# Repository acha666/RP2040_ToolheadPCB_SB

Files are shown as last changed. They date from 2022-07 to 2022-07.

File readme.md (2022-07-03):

# Stealthburner_Toolhead_PCB

<font size=5>[中文文档/Chinese Document](readme_cn.md)</font>

**The Project has not finished**

## Overview
This project contains a 3Dprinter Toolhead PCB for VORON StealthBurner Toolhead

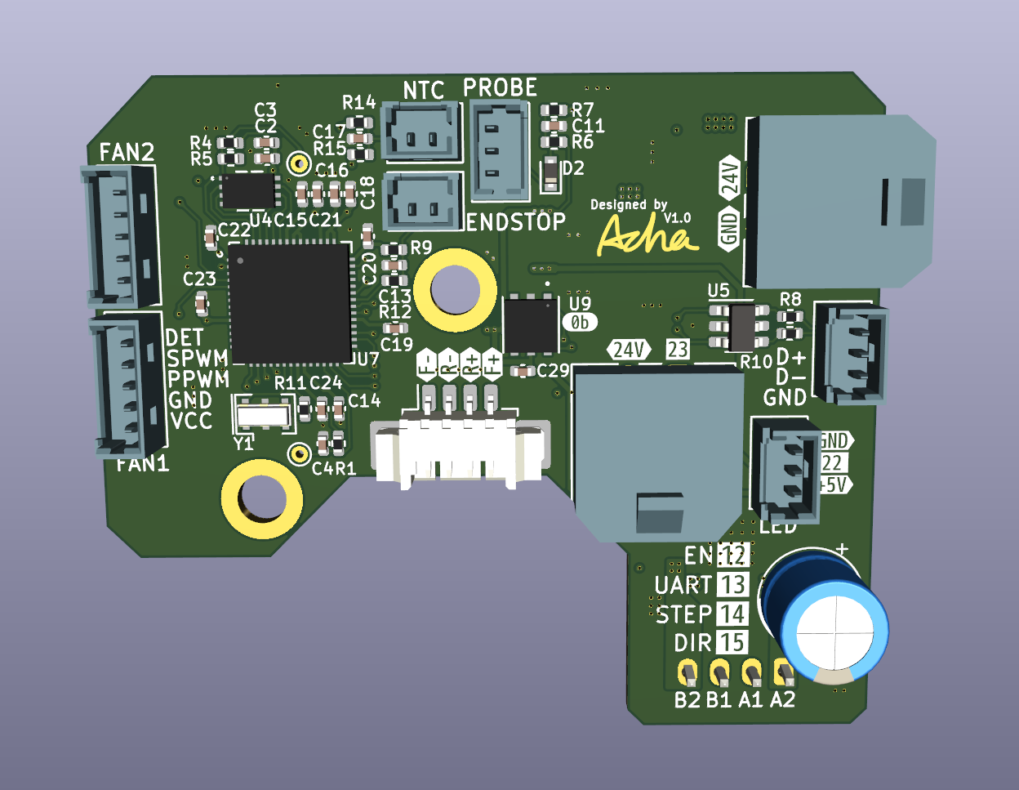
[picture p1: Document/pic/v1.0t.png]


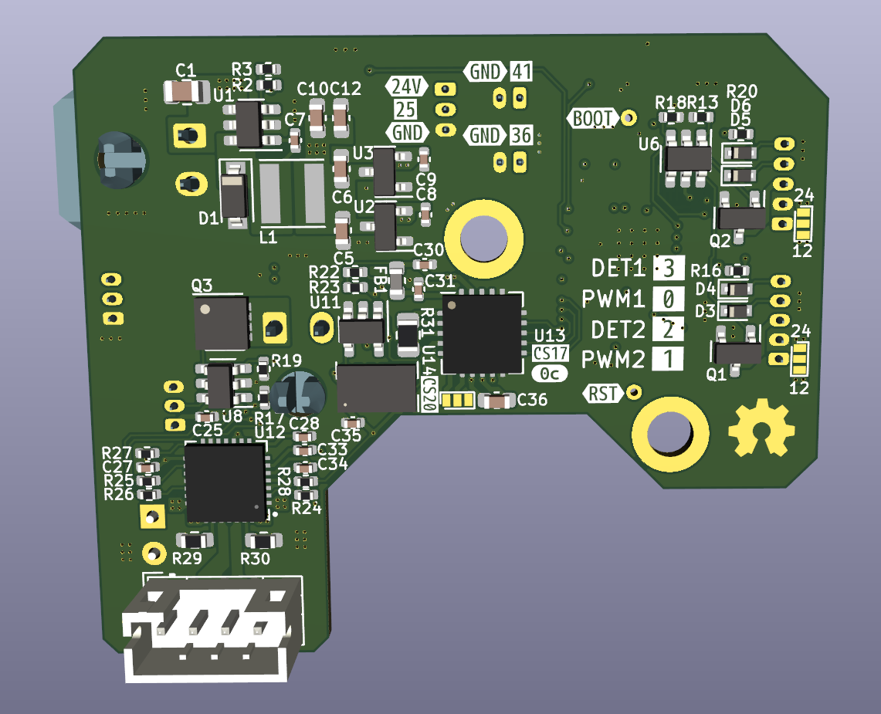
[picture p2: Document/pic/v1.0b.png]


The board has

* RP2040 Microcontroller, connect to Raspberry PI with USB
* TMC2209 for extruder motor
* MAX31865 RTD-to-Digital Converter
* SHT20 humidity&temperature sensor
* ADXL345 accrometer
* Two 5pins fan connecter, fit with 2/3/4 wires, 12/24V fans
* A 3pins probe connecter
* A normal NTC Thermistor connector
* A 2pins X Endstop connector
* A 3pins 5V WS2812(Neopixel) LED connector
* A 24V heater connector

## [Config Referencce](klipper_config.cfg)

## [Programming Guide](Document/programming.md)

## Details
### Microcontroller
You can easily buy a RP2040 chip by about 1USD, it's much cheaper than similar STM32 series MCU today

the RP2040 has some UART interfaces ans a USB port, the USB is used for this design

### MAX31865
the on-board MAX31865 chip supports 2/3/4 wires, PT100/PT1000 RTD. please notice that you should choose the reference resistor(430R/4.3K) and a capacitor(100nF/1uF) based on your RTD value. If you use an 3wire RTD, please connect the FORCE2 pin to PORCE+, otherwise connect it to GND. Please make sure that your wiring is correct. Check the [Datasheet](https://datasheets.maximintegrated.com/en/ds/MAX31865.pdf) and [Here](Document/max31865.md) for more information.

### SHT20
This sensor is used to monitor chamber temp.

Though SHT20 is an NRND product now, we have no choice because klipper frimware only support SHT20. DS18B20 sensors are only supported on the "host mcu". A NTC thermistor should work too, so if a RTD sensor is used to measure hotend temp, you can have a try.

### ADXL345
is for resonances measurement. Both ADXL343 and ADXL345 should work

### FAN Connecter
support 2wires, 3wires(with speed monitor pin), 4wires(with PWM input and speed monitor)

12V/24V voltage can be set by the jumper. Check [Here](Document/fan.md) for more information.

### Heater
be careful about selection on MOSFET, a N-Channel MOSFET with low RDSon at 4.5V

### DC-DC
many models can be used, as long as they have same pin out

The inductor is 4x4mm package, as slim as possible(under 2mm height)

You may choose
* WPN4012H (Sunlord)
* SPH4012S PH4018 (Sunlord)
* SWPA4010 SWPA4018 SWPA4020 (Sunlord)
* SLW4010 (Sunltech)
* FHD4012 (cjiang)

| Buck converter options |
| --- |
| BL9342(by Shanghai Belling) |
| LMR54410(by TI)(Not tested) |
| LMR14006(by TI)(Not tested) |

please check the schmatic for details

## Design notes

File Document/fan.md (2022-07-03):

# Fan Wiring

There are five pins in connecter, they are

* frequency generation waveform input
* PWM **signal** output
* PWM **power** output
* ground
* power

For those fans they have own PWM signal input, the PWM **power** output is unused

# 2 Wires
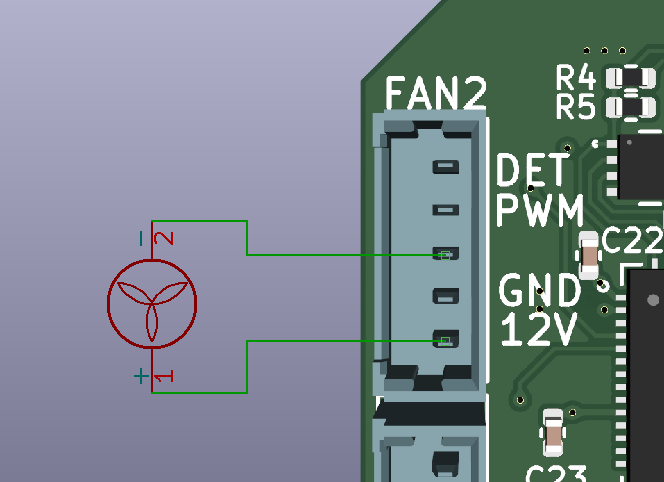
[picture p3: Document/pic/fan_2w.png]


# 3 Wires
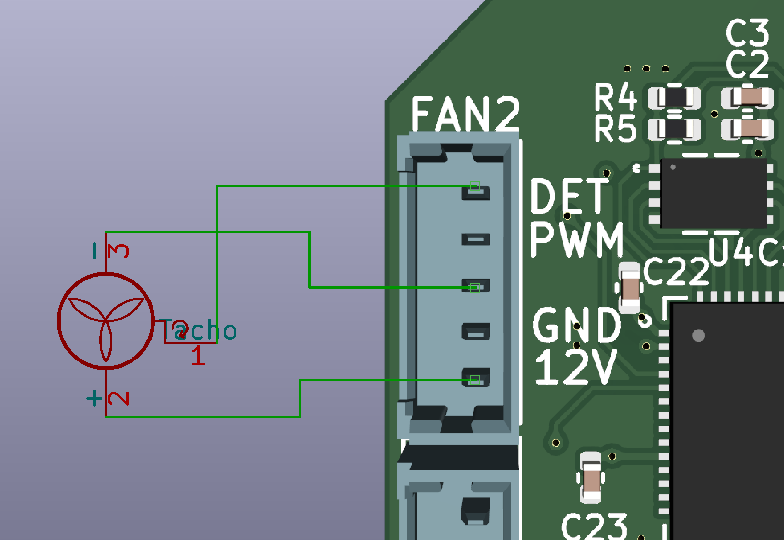
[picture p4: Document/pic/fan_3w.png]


# 4 Wires
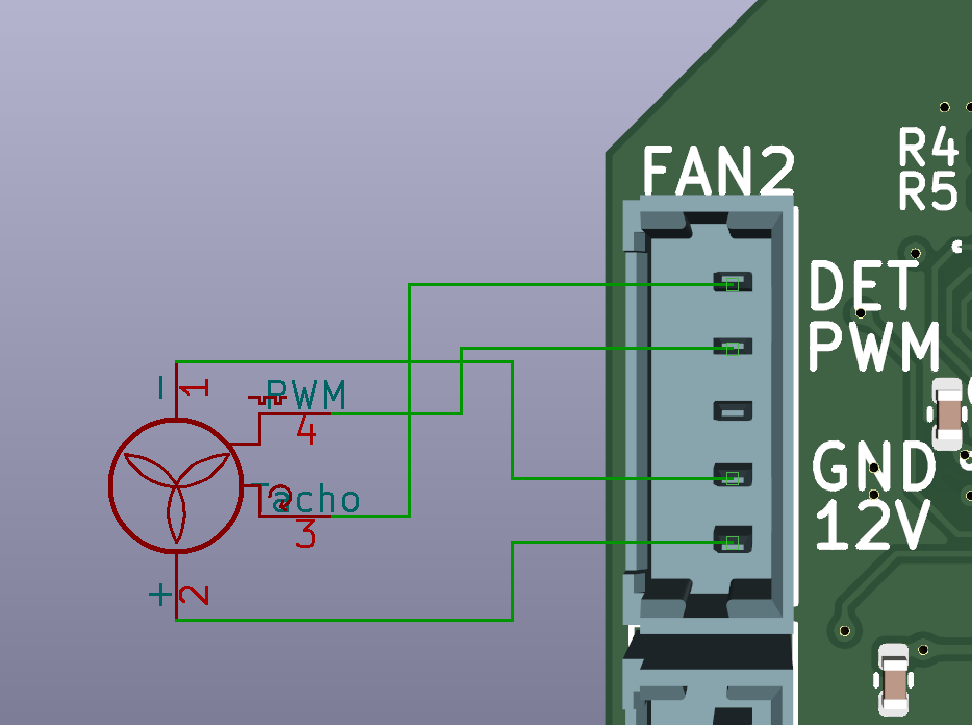
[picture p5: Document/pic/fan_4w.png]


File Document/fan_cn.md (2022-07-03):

# 风扇接线

风扇接口五个引脚，分别是

* 转速检测方波输入
* PWM**信号**输出
* PWM**功率**输出
* 地
* 供电

对于有PWM信号输入的风扇，用不到PWM功率输出的，MOS管等可以不贴

# 二线


# 三线


# 四线


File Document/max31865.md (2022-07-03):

# For Different Wire Number

## 2 Wires
connect Force2 to ground, they are pin2&3 for the jumper

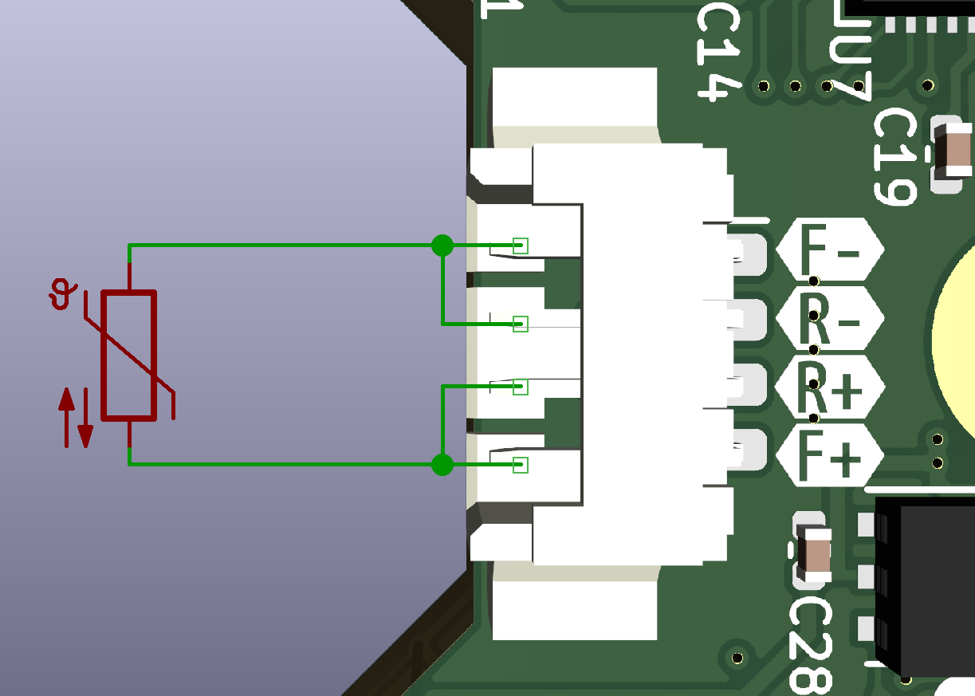
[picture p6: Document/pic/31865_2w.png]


## 3 Wires
connect Force2 to Force+, they are pin1&2 for the jumper

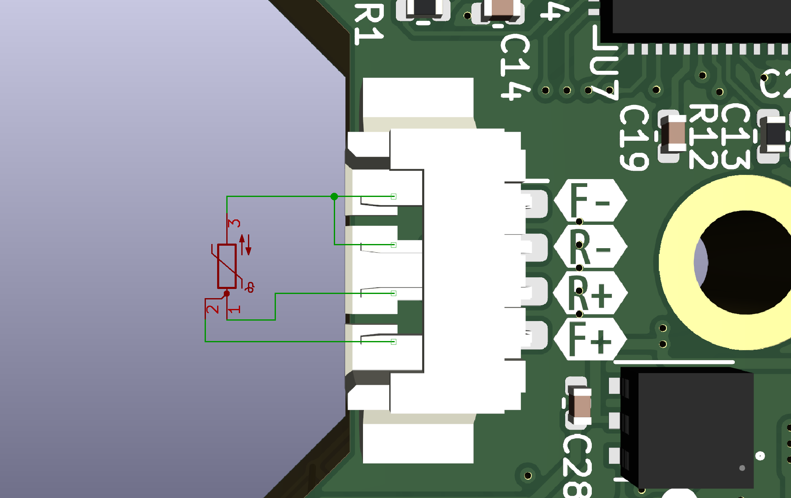
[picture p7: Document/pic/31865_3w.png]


## 4 Wires
connect Force2 to ground, they are pin2&3 for the jumper

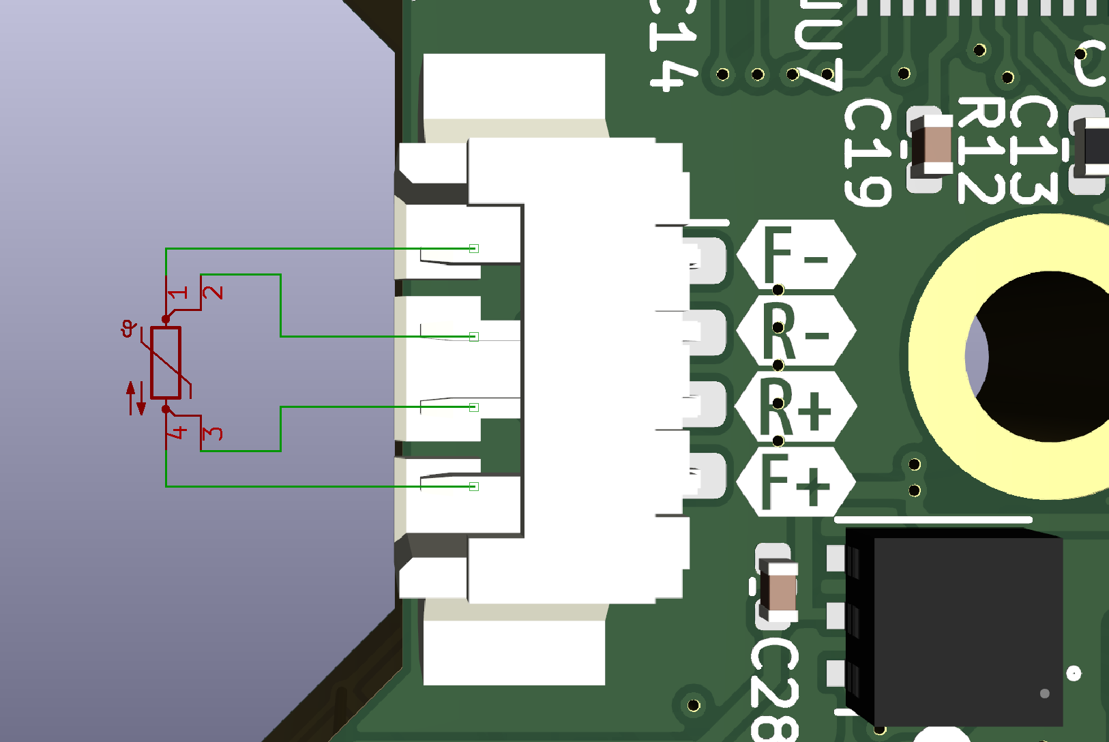
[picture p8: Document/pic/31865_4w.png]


# For Different RTD Value
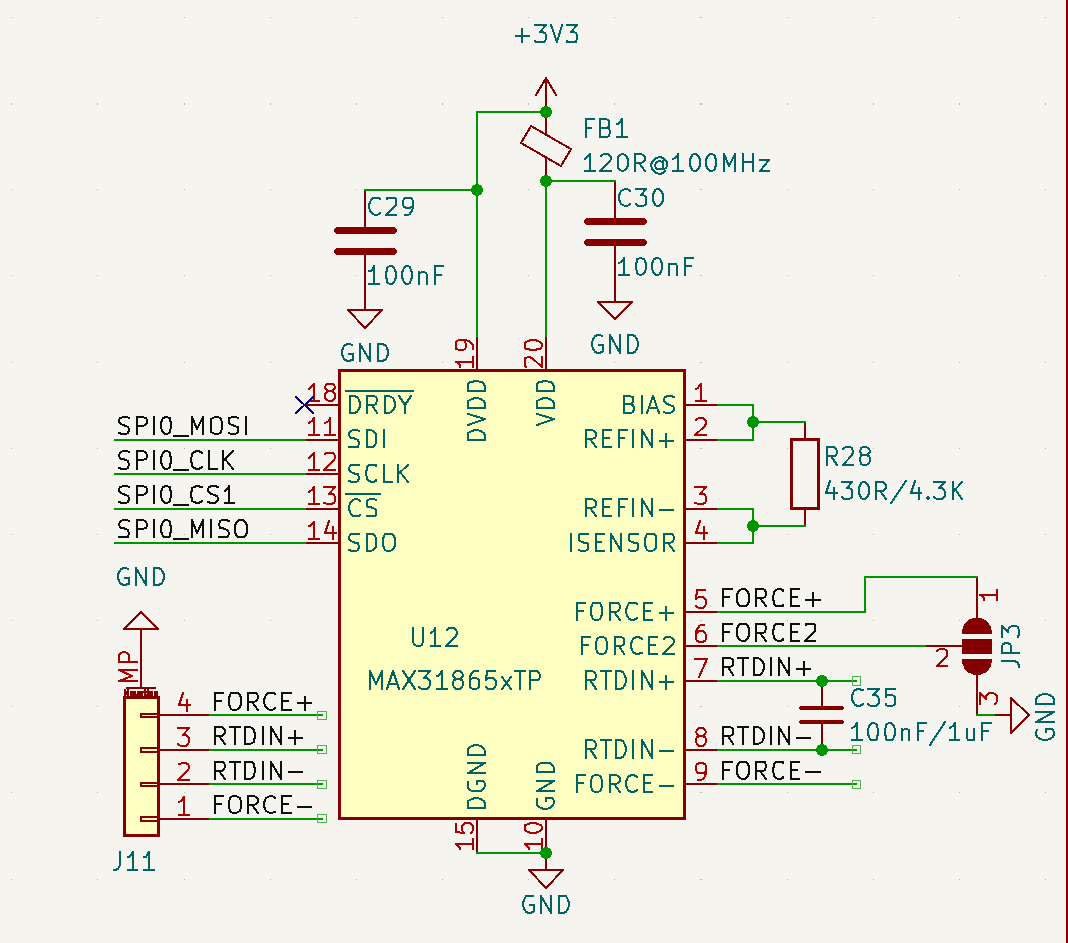
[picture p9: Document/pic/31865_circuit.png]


the R28 in picthre is reference resistor, C35 is the Capacitor

Please choose High-quality, High-precision and Low-temperature-drift resistor

But actually a normal 1% resistor work well too

| RTD | Resistance | Capacitance |
|-----|-----|---|
|PT100 | 430R|100nF|
|PT1000|4.3K|1uF|

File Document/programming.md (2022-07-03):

# Programming

The board has two testpoints, they are for boot select and reset

Connecting the boot testpoint to ground makes mcu boot from bootloader

Connecting the reset testpoint to ground makes mcu reset

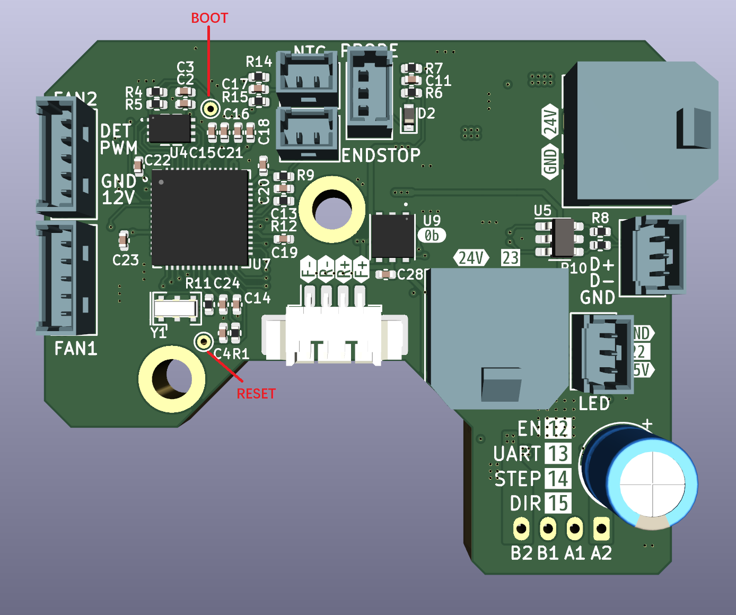
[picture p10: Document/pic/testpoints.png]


Check [User Manual of BigTreeTech SKR-PICO](https://github.com/bigtreetech/SKR-Pico) for more information

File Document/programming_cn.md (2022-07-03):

# 程序烧录

板上引出了复位测试点和启动选择测试点，如图



短接RST到地使MCU复位，在复位时短接BOOT到地启动到Bootloader进行程序烧录

若有疑问请参考[BigTreeTech SKR-PICO 用户手册](https://github.com/bigtreetech/SKR-Pico)

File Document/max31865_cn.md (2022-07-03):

# 不同线制

## 2线
短接Force2到地，即跳线23脚

如图连接



## 3线
短接Force2到Force+，即跳线12脚

如图连接



## 4线
短接Force2到地，即跳线23脚

如图连接



# 不同铂电阻阻值

图中R28为参考电阻，C35为电容

参考电阻请选择高质量、高精度、低温漂的电阻，当然预算有限1%又不是不能用

| 类型 | 阻值 | 容值 |
|-----|-----|---|
|PT100 | 430R|100nF|
|PT1000|4.3K|1uF|

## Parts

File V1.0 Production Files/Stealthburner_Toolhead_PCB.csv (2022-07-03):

Designator | Qnty | Comment | Footprint
C1, | 1 | 22uF/35V | Capacitor_SMD:C_0805_2012Metric
C2, | 1 | 2.2uF | Capacitor_SMD:C_0402_1005Metric
C3, C4, C7, C11, C13, C14, C15, C19, C20, C21, C22, C23, C24, C25, C27, C29, C30, C31, C33, C35, | 20 | 100nF | Capacitor_SMD:C_0402_1005Metric
C5, C6, | 2 | 10uF | Capacitor_SMD:C_0603_1608Metric
C8, C9, C17, | 3 | 10uF | Capacitor_SMD:C_0402_1005Metric
C10, C12, | 2 | 22uF | Capacitor_SMD:C_0603_1608Metric
C16, C18, | 2 | 1uF | Capacitor_SMD:C_0402_1005Metric
C28, | 1 | 4.7uF | Capacitor_SMD:C_0402_1005Metric
C32, | 1 | 100uF | Capacitor_THT:CP_Radial_D6.3mm_P2.50mm
C34, | 1 | 22nF | Capacitor_SMD:C_0402_1005Metric
C36, | 1 | 100nF/1uF | Capacitor_SMD:C_0603_1608Metric
D1, | 1 | CUS10S30 | Diode_SMD:D_SOD-123
D2, | 1 | 1N4148WT | Diode_SMD:D_SOD-523
D3, D5, | 2 | 1N4148 | Diode_SMD:D_SOD-523
D4, D6, | 2 | D_TVS | Diode_SMD:D_SOD-523
FB1, | 1 | 120R@100MHz | Inductor_SMD:L_0603_1608Metric
H1, H2, | 2 | MountingHole | 1_Library:MountingHole_3mm_Pad
J1, J9, | 2 | Conn_01x02 | 1_Library:Molex_Micro-Fit_3.0_43650-0200_1x02_P3.00mm_Horizontal
J2, J5, J8, | 3 | Conn_01x03 | 1_Library:Molex_PicoBlade_53047-0310_1x03_P1.25mm_Vertical
J3, | 1 | TestPoint | TestPoint:TestPoint_THTPad_D1.0mm_Drill0.5mm
J4, J6, | 2 | Conn_01x02 | 1_Library:Molex_PicoBlade_53047-0210_1x02_P1.25mm_Vertical
J7, J10, | 2 | Conn_01x05 | 1_Library:Molex_PicoBlade_53047-0510_1x05_P1.25mm_Vertical
J11, | 1 | Conn_01x04 | Connector_Molex:Molex_PicoBlade_53261-0471_1x04-1MP_P1.25mm_Horizontal
J12, | 1 | Conn_01x04 | Connector_JST:JST_PH_B4B-PH-K_1x04_P2.00mm_Vertical
JP1, JP2, | 2 | SolderJumper_3_Open | 1_Library:SolderJumper-3_P1.3mm_Open_Pad1.0x1.5mm
JP3, | 1 | 1_Library:SolderJumper-3_P1.3mm_Open_Pad1.0x1.5mm | 1_Library:SolderJumper-3_P1.3mm_Open_Pad1.0x1.5mm
L1, | 1 | 6.2uH | Inductor_SMD:L_Taiyo-Yuden_NR-40xx
Q1, Q2, | 2 | AO3400A | Package_TO_SOT_SMD:SOT-23
Q3, | 1 | WSD4038DN | Package_SON:VSON-8_3.3x3.3mm_P0.65mm_NexFET
R1, R6, R9, R13, R16, R17, R18, R19, R20, R22, R23, | 11 | 10K | Resistor_SMD:R_0402_1005Metric
R2, | 1 | 124K | Resistor_SMD:R_0402_1005Metric
R3, | 1 | 8.87K | Resistor_SMD:R_0402_1005Metric
R4, | 1 | NC | Resistor_SMD:R_0402_1005Metric
R5, R11, | 2 | 1K | Resistor_SMD:R_0402_1005Metric
R7, R12, R14, R24, R25, R26, | 6 | 100R | Resistor_SMD:R_0402_1005Metric
R8, R10, | 2 | 27R | Resistor_SMD:R_0402_1005Metric
R15, | 1 | 4.7K | Resistor_SMD:R_0402_1005Metric
R27, R28, | 2 | 20K | Resistor_SMD:R_0402_1005Metric
R29, R30, | 2 | 0R11 | Resistor_SMD:R_0603_1608Metric
R31, | 1 | 430R/4.3K | Resistor_SMD:R_0805_2012Metric
TP1, | 1 | TestPoint | TestPoint:TestPoint_THTPad_D1.0mm_Drill0.5mm
U1, | 1 | BL9342 | Package_TO_SOT_SMD:SOT-23-6
U2, | 1 | ME6209A50M3G | Package_TO_SOT_SMD:SOT-23
U3, | 1 | ME6209A33M3G | Package_TO_SOT_SMD:SOT-23
U4, | 1 | W25Q16JVUXIQ | 1_Library:W25Q16JVUXIQ
U5, | 1 | USBLC6-2SC6 | Package_TO_SOT_SMD:SOT-23-6
U6, U8, | 2 | 74LVC2G17 | Package_TO_SOT_SMD:SOT-23-6
U7, | 1 | RP2040 | 1_Library:RP2040TR7
U9, | 1 | SHT20 | 1_Library:SHT20
U11, | 1 | 74LVC1G32 | Package_TO_SOT_SMD:SOT-23-5
U12, | 1 | TMC2209-LA-T | 1_Library:TMC2209-LA-T
U13, | 1 | MAX31865xTP | Package_DFN_QFN:TQFN-20-1EP_5x5mm_P0.65mm_EP3.25x3.25mm
U14, | 1 | ADXL343 | Package_LGA:LGA-14_3x5mm_P0.8mm_LayoutBorder1x6y
Y1, | 1 | CSTNE12M0 | Crystal:Resonator_SMD_Murata_CSTxExxV-3Pin_3.0x1.1mm

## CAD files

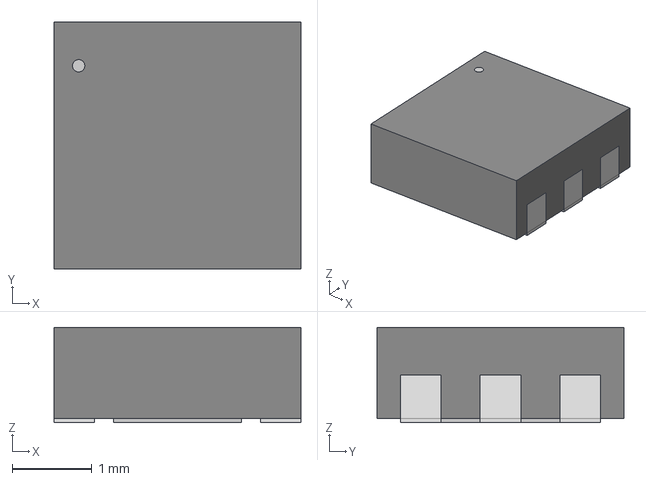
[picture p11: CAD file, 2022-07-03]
Hardware/3D/1-100706-01_SEN.step
3.10 x 3.10 x 1.20 mm

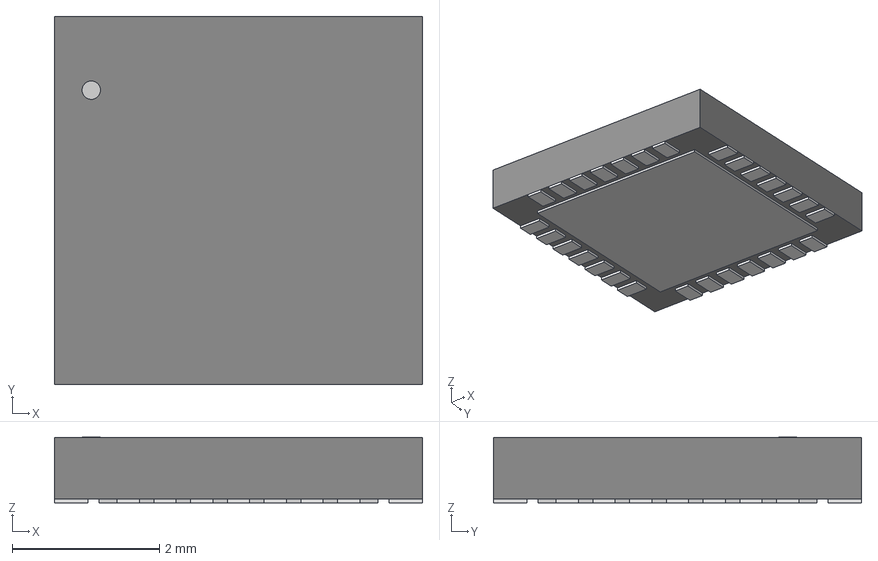
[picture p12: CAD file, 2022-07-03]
Hardware/3D/QFN28_5X5_3X8_EPAD_TRI.step
5.00 x 5.00 x 0.892 mm

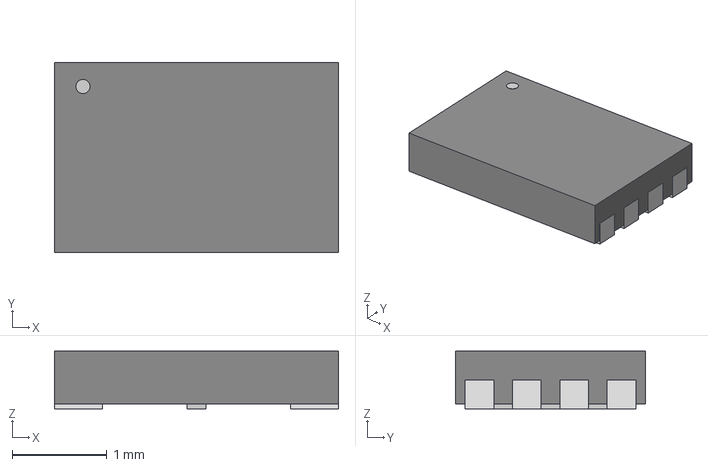
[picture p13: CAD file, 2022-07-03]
Hardware/3D/W25Q16JVUXIQ_WIN.step
3.00 x 2.01 x 0.612 mm

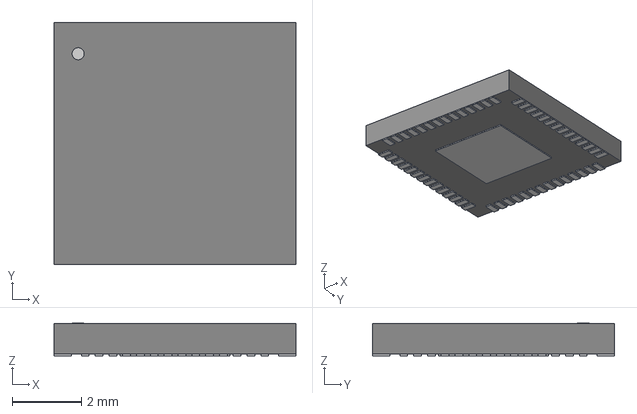
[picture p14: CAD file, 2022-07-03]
Hardware/3D/RP2040TR7_RPI.step
7.01 x 7.01 x 0.942 mm

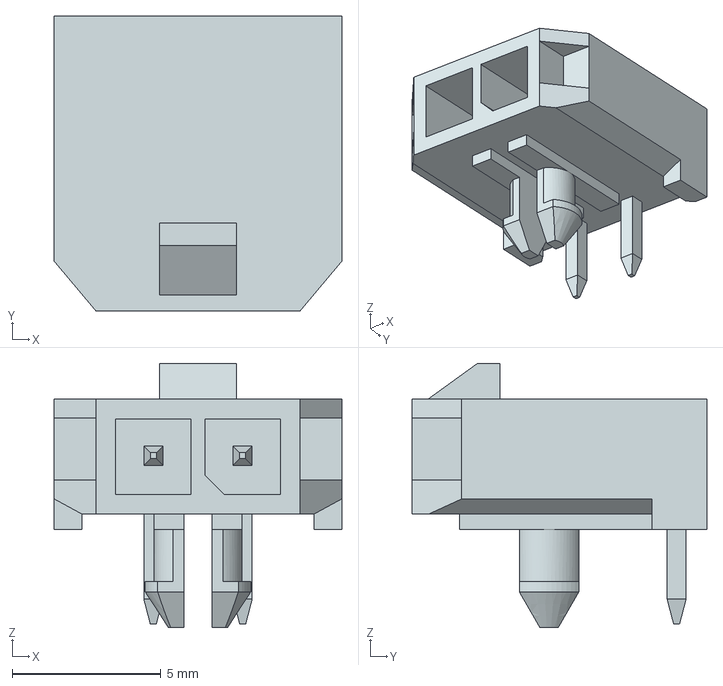
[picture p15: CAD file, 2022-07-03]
Hardware/3D/436500200.stp
9.65 x 9.90 x 8.87 mm

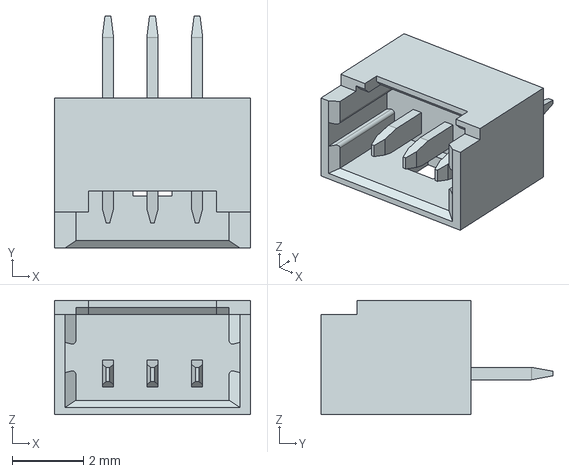
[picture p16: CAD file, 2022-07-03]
Hardware/3D/530470310.stp
5.50 x 6.50 x 3.20 mm

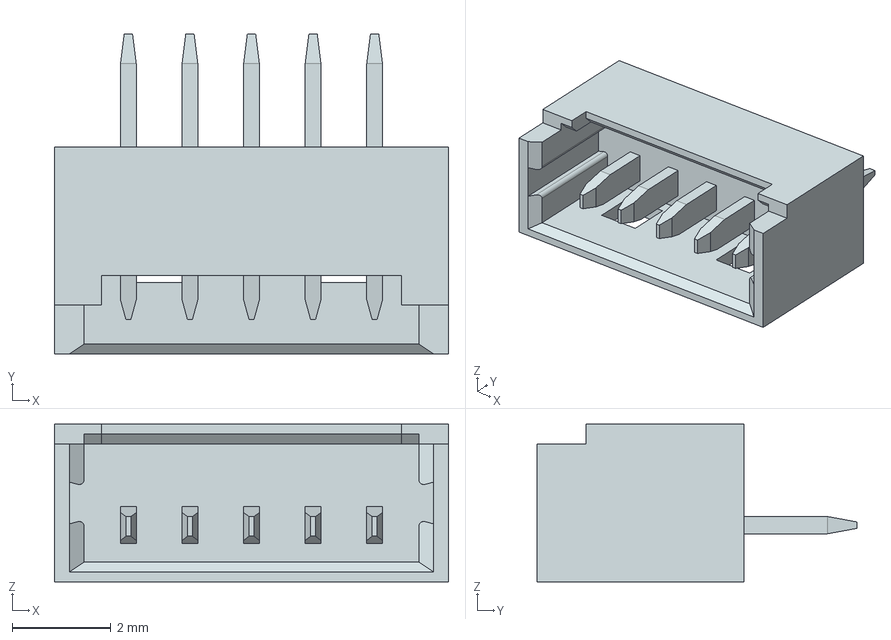
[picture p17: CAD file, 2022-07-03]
Hardware/3D/530470510.stp
8.00 x 6.50 x 3.20 mm

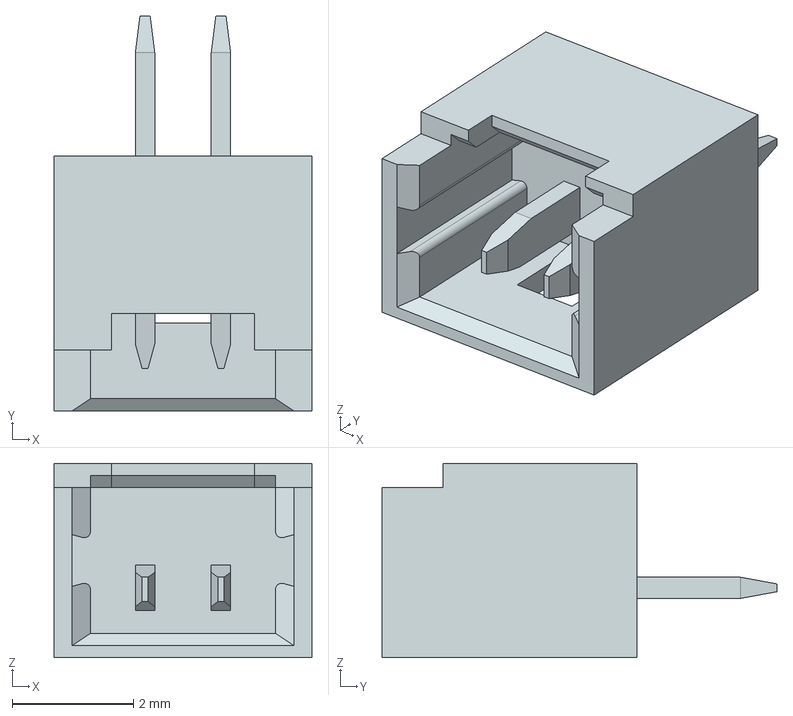
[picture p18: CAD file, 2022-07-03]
Hardware/3D/530470210.stp
4.25 x 6.50 x 3.20 mm

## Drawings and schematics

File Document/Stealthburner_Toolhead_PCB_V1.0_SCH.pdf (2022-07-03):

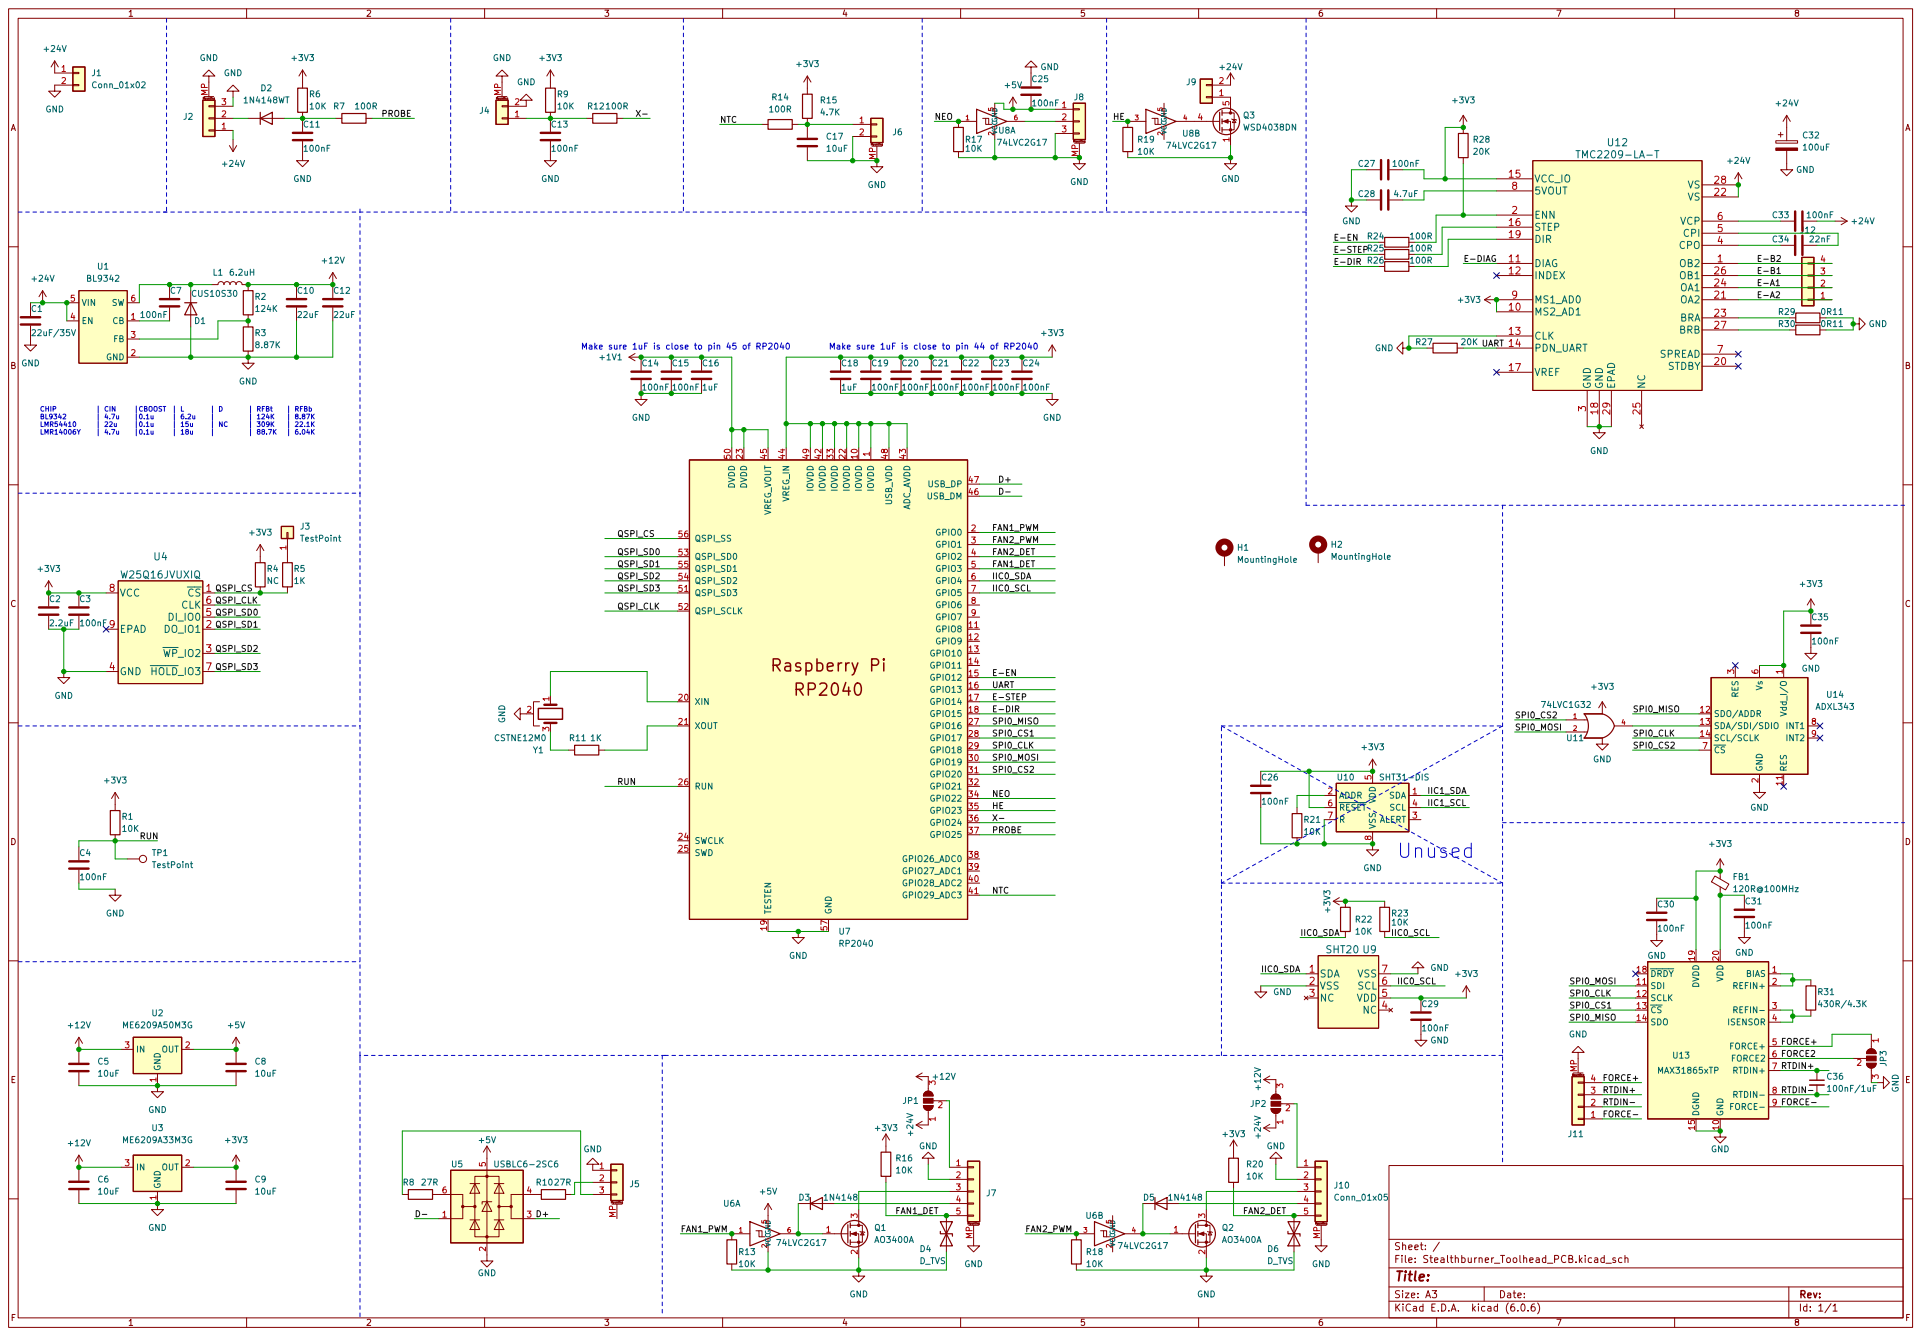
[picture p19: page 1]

CHIP | CIN |CBOOST | L | D | RFBt | RFBb BL9342 | 4.7u |0.1u | 6.2u | | 124K | 8.87K

1 IOVDD 10 GPIO8 11 GPIO9 12 GPIO10 13 GPIO11 14 GPIO12 15 GPIO13 16 GPIO14 17 GPIO15 18 TESTEN 19 GPIO0 2 XIN 20 XOUT 21 IOVDD 22 DVDD 23 SWCLK 24 SWD 25 RUN 26 GPIO16 27 GPIO17 28 GPIO18 29 GPIO1 3 GPIO19 30 GPIO20 31 GPIO21 32 IOVDD 33 GPIO22 34 GPIO23 35 GPIO24 36 GPIO25 37 GPIO26_ADC0 38 GPIO27_ADC1 39 GPIO2 4 GPIO28_ADC2 40 GPIO29_ADC3 41 IOVDD 42 ADC_AVDD 43 VREG_IN 44 VREG_VOUT 45 USB_DM 46 USB_DP 47 USB_VDD 48 IOVDD 49 GPIO3 5 DVDD 50 QSPI_SD3 51 QSPI_SCLK 52 QSPI_SD0 53 QSPI_SD2 54 QSPI_SD1 55 QSPI_SS 56 GND 57 GPIO4 6 GPIO5 7 GPIO6 8 GPIO7 9 U7RP2040 +3V3

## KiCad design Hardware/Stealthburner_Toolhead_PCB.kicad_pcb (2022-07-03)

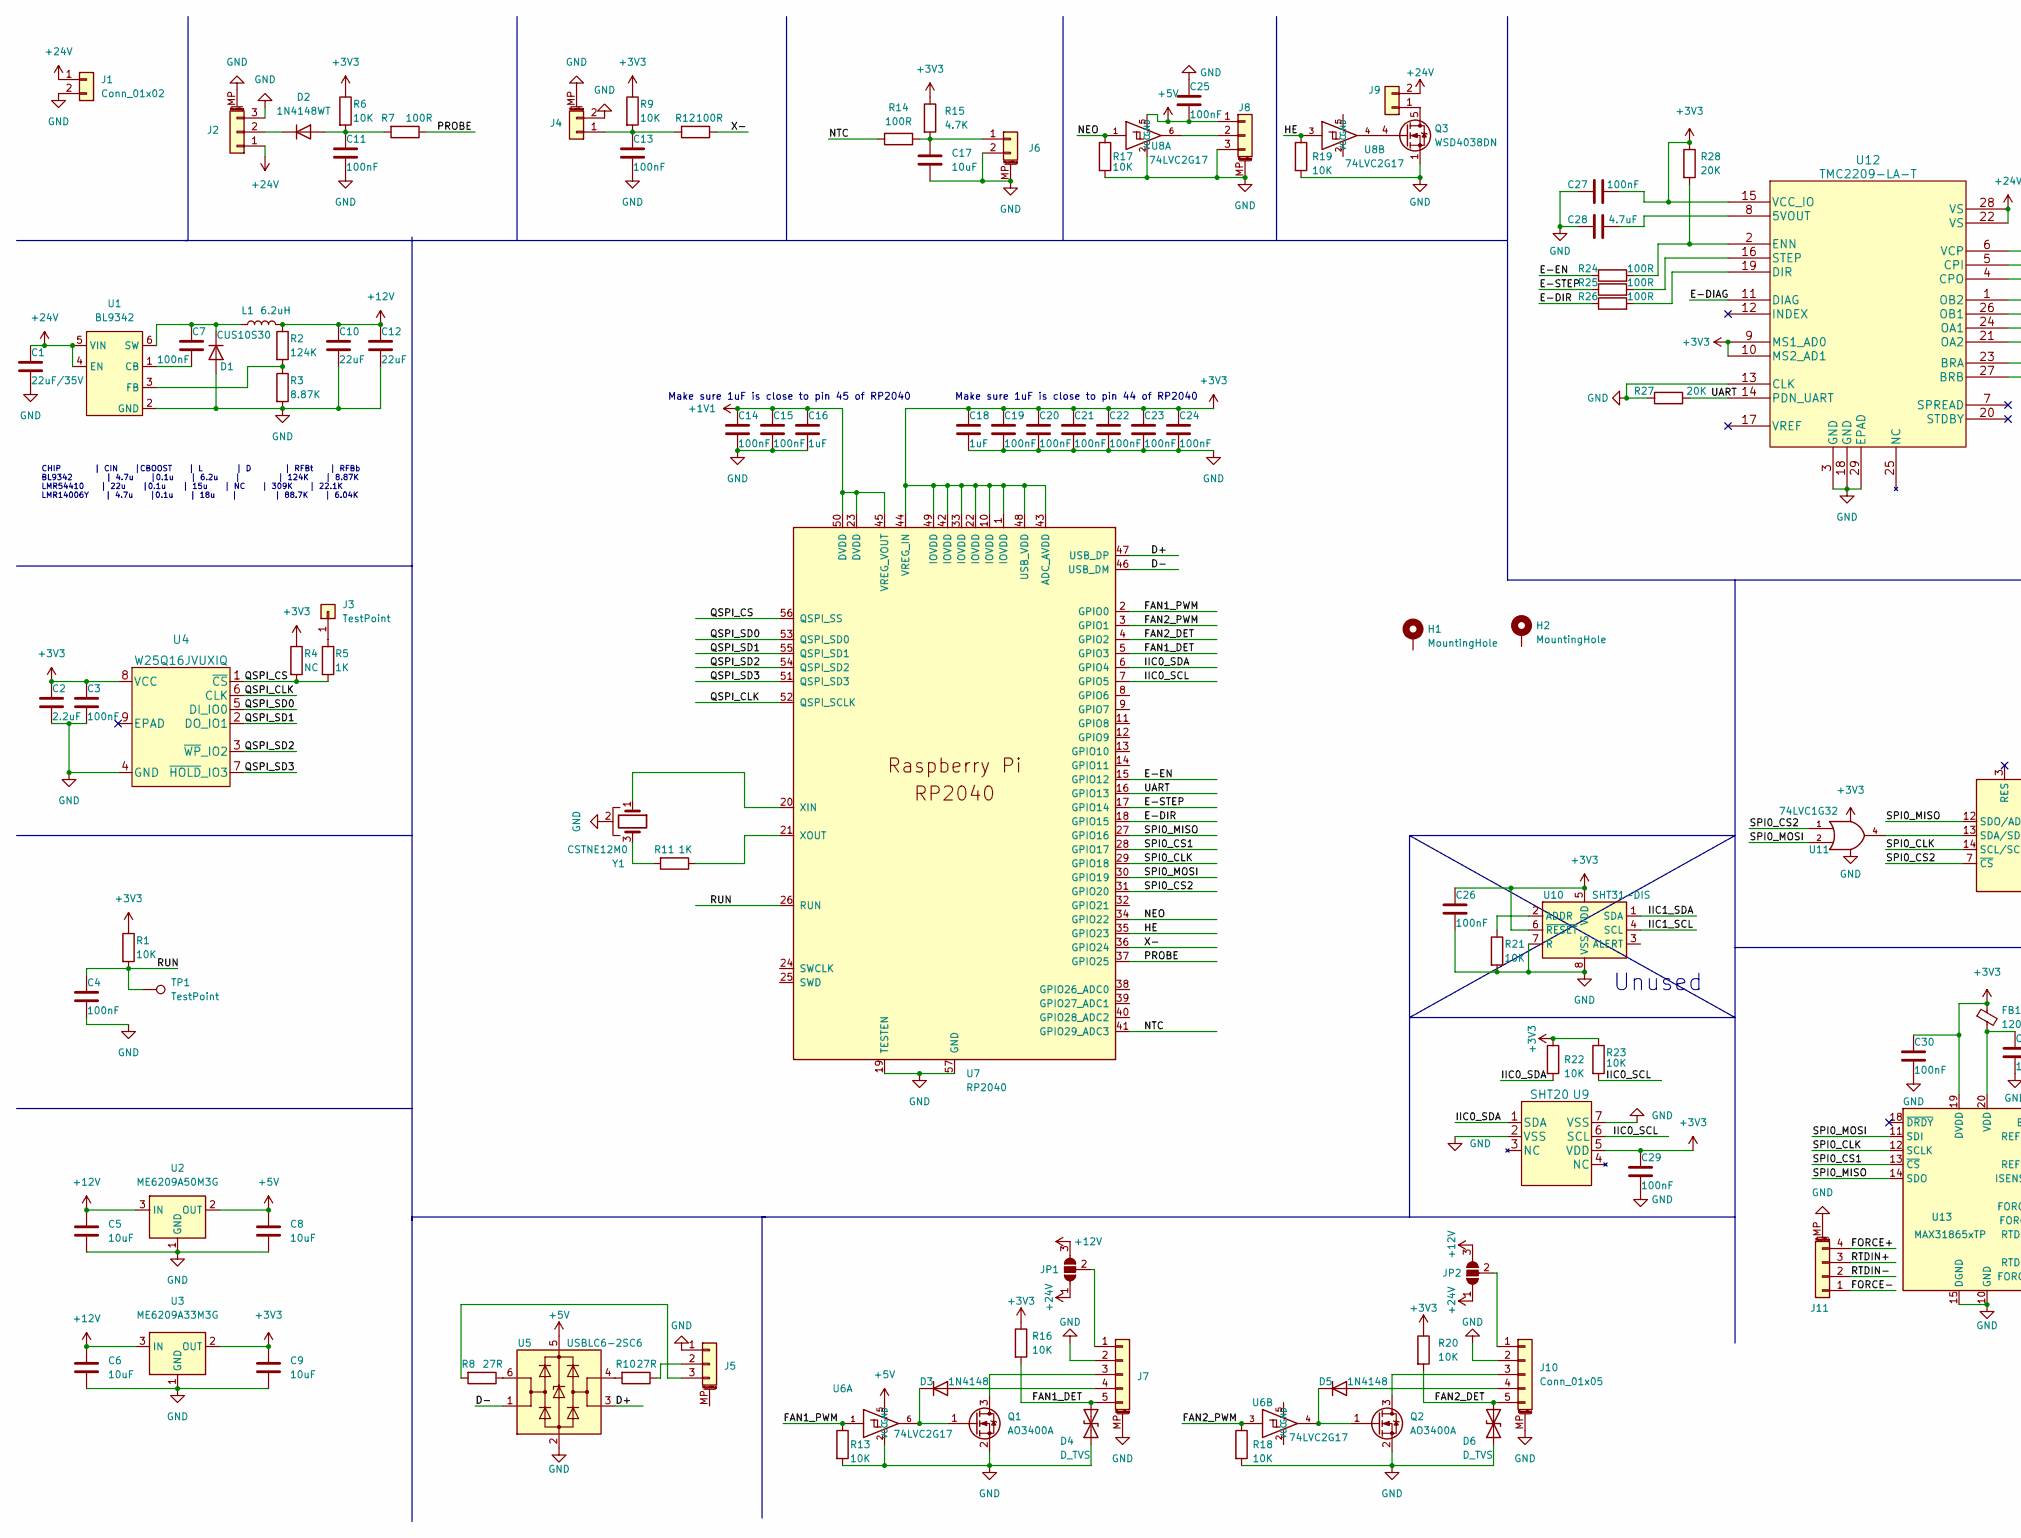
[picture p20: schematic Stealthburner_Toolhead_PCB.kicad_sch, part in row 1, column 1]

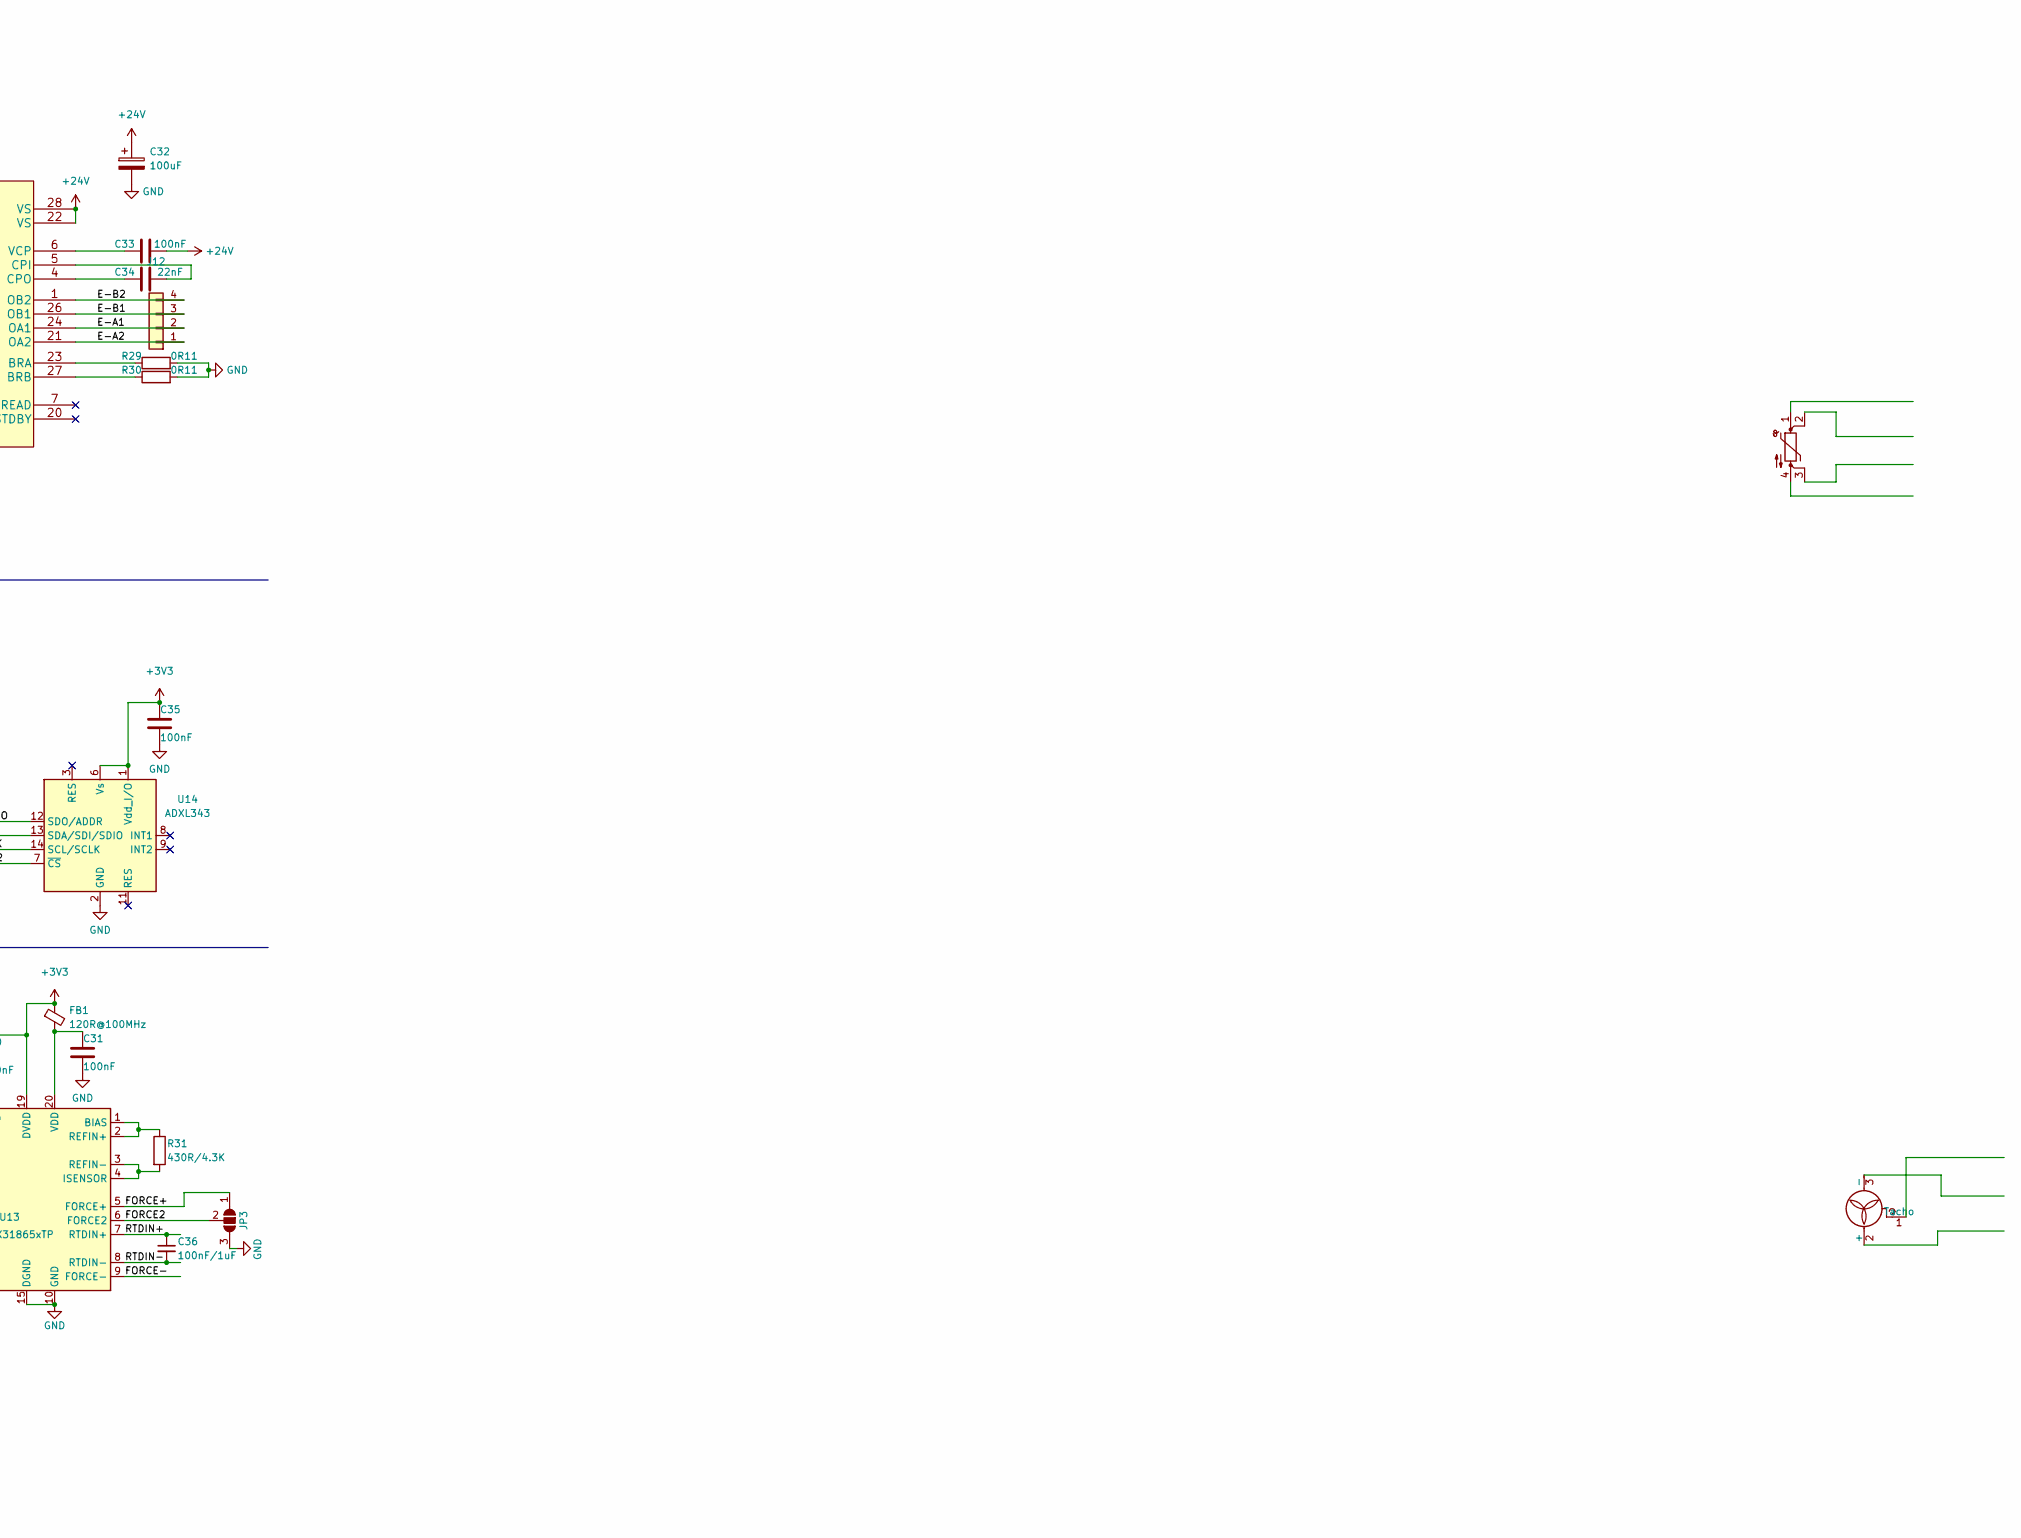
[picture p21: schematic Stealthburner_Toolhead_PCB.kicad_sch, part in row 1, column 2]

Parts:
C1: 22uF/35V; C_0805_2012Metric
C2: 2.2uF; C_0402_1005Metric
C3, C4, C7, C11, C13, C14, C15, C19, C20, C21, C22, C23, C24, C25, C26, C27, C29, C30, C31, C33, C35: 100nF; C_0402_1005Metric
C5, C6: 10uF; C_0603_1608Metric
C8, C9, C17: 10uF; C_0402_1005Metric
C10, C12: 22uF; C_0603_1608Metric
C16, C18: 1uF; C_0402_1005Metric
C28: 4.7uF; C_0402_1005Metric
C32: 100uF; CP_Radial_D6.3mm_P2.50mm
C34: 22nF; C_0402_1005Metric
C36: 100nF/1uF; C_0603_1608Metric
D1: CUS10S30; D_SOD-123
D2: 1N4148WT; D_SOD-523
D3, D5: 1N4148; D_SOD-523
D4, D6: D_TVS; D_SOD-523
FB1: 120R@100MHz; L_0603_1608Metric
H1, H2: MountingHole; MountingHole_3mm_Pad
J1, J9: Conn_01x02; Molex_Micro-Fit_3.0_43650-0200_1x02_P3.00mm_Horizontal
J2, J5, J8: Conn_01x03; Molex_PicoBlade_53047-0310_1x03_P1.25mm_Vertical
J3: TestPoint; TestPoint_THTPad_D1.0mm_Drill0.5mm
J4, J6: Conn_01x02; Molex_PicoBlade_53047-0210_1x02_P1.25mm_Vertical
J7, J10: Conn_01x05; Molex_PicoBlade_53047-0510_1x05_P1.25mm_Vertical
J11: Conn_01x04; Molex_PicoBlade_53261-0471_1x04-1MP_P1.25mm_Horizontal
J12: Conn_01x04; JST_PH_B4B-PH-K_1x04_P2.00mm_Vertical
JP1, JP2: SolderJumper_3_Open; SolderJumper-3_P1.3mm_Open_Pad1.0x1.5mm
JP3: 1_Library:SolderJumper-3_P1.3mm_Open_Pad1.0x1.5mm; SolderJumper-3_P1.3mm_Open_Pad1.0x1.5mm
L1: 6.2uH; L_Taiyo-Yuden_NR-40xx
M1: Fan_3pin
Q1, Q2: AO3400A; SOT-23
Q3: WSD4038DN; VSON-8_3.3x3.3mm_P0.65mm_NexFET
R1, R6, R9, R13, R16, R17, R18, R19, R20, R21, R22, R23: 10K; R_0402_1005Metric
R2: 124K; R_0402_1005Metric
R3: 8.87K; R_0402_1005Metric
R4: NC; R_0402_1005Metric
R5, R11: 1K; R_0402_1005Metric
R7, R12, R14, R24, R25, R26: 100R; R_0402_1005Metric
R8, R10: 27R; R_0402_1005Metric
R15: 4.7K; R_0402_1005Metric
R27, R28: 20K; R_0402_1005Metric
R29, R30: 0R11; R_0603_1608Metric
R31: 430R/4.3K; R_0805_2012Metric
TH1: Thermistor_NTC_4Wire
TP1: TestPoint; TestPoint_THTPad_D1.0mm_Drill0.5mm
U1: BL9342; SOT-23-6
U2: ME6209A50M3G; SOT-23
U3: ME6209A33M3G; SOT-23
U4: W25Q16JVUXIQ
U5: USBLC6-2SC6; SOT-23-6
U6, U8: 74LVC2G17; SOT-23-6
U7: RP2040; RP2040TR7
U9: SHT20
U10: SHT31-DIS; Sensirion_DFN-8-1EP_2.5x2.5mm_P0.5mm_EP1.1x1.7mm
U11: 74LVC1G32; SOT-23-5
U12: TMC2209-LA-T
U13: MAX31865xTP; TQFN-20-1EP_5x5mm_P0.65mm_EP3.25x3.25mm
U14: ADXL343; LGA-14_3x5mm_P0.8mm_LayoutBorder1x6y
Y1: CSTNE12M0; Resonator_SMD_Murata_CSTxExxV-3Pin_3.0x1.1mm

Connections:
+1V1: C14.1, C15.1, C16.1, U7.23 (DVDD), U7.45 (VREG_VOUT), U7.50 (DVDD)
+3V3: C2.1, C3.1, C9.1, C18.1, C19.1, C20.1, C21.1, C22.1, C23.1, C24.1, C26.1, C27.2, C29.1, C30.1, C35.1, FB1.1, R1.1, R4.1, R6.1, R9.1, R15.1, R16.1, R20.1, R22.1, R23.1, R28.1, U3.2 (OUT), U4.8 (VCC), U7.1 (IOVDD), U7.10 (IOVDD), U7.22 (IOVDD), U7.33 (IOVDD), U7.42 (IOVDD), U7.43 (ADC_AVDD), U7.44 (VREG_IN), U7.48 (USB_VDD), U7.49 (IOVDD), U9.5 (VDD), U10.5 (VDD), U10.6 (~RESET), U11.5 (VCC), U12.9 (MS1_AD0), U12.10 (MS2_AD1), U12.15 (VCC_IO), U13.19 (DVDD), U14.1 (Vdd_I/O), U14.6 (Vs)
+5V: C8.1, C25.2, J8.1, U2.2 (OUT), U5.5 (VBUS), U6.5 (VCC), U8.5 (VCC)
+12V: C5.1, C6.1, C10.1, C12.1, JP1.3 (B), JP2.3 (B), L1.2, R2.1, U2.3 (IN), U3.3 (IN)
+24V: C1.1, C32.1, C33.2, J1.1, J2.1, J9.2, JP1.1 (A), JP2.1 (A), U1.4 (EN), U1.5 (VIN), U12.22 (VS), U12.28 (VS)
/D+: U5.3 (I/O2), U7.47 (USB_DP)
/D-: U5.1 (I/O1), U7.46 (USB_DM)
/E-A1: J12.2, U12.24 (OA1)
/E-A2: J12.1, U12.21 (OA2)
/E-B1: J12.3, U12.26 (OB1)
/E-B2: J12.4, U12.1 (OB2)
/E-DIAG: U12.11 (DIAG)
/E-DIR: R26.1, U7.18 (GPIO15)
/E-EN: R24.1, U7.15 (GPIO12)
/E-STEP: R25.1, U7.17 (GPIO14)
/FAN1_DET: D4.2 (A2), J7.5, R16.2, U7.5 (GPIO3)
/FAN1_PWM: R13.1, U6.1, U7.2 (GPIO0)
/FAN2_DET: D6.2 (A2), J10.5, R20.2, U7.4 (GPIO2)
/FAN2_PWM: R18.1, U6.3, U7.3 (GPIO1)
/FORCE2: JP3.2 (C), U13.6 (FORCE2)
/FORCE+: J11.4, JP3.1 (A), U13.5 (FORCE+)
/FORCE-: J11.1, U13.9 (FORCE-)
/HE: R19.1, U7.35 (GPIO23), U8.3
/IIC0_SCL: R23.2, U7.7 (GPIO5), U9.6 (SCL)
/IIC0_SDA: R22.2, U7.6 (GPIO4), U9.1 (SDA)
/NEO: R17.1, U7.34 (GPIO22), U8.1
/NTC: R14.1, U7.41 (GPIO29_ADC3)
/PROBE: R7.1, U7.37 (GPIO25)
/QSPI_CLK: U4.6 (CLK), U7.52 (QSPI_SCLK)
/QSPI_CS: R4.2, R5.2, U4.1 (~CS), U7.56 (QSPI_SS)
/QSPI_SD0: U4.5 (DI_IO0), U7.53 (QSPI_SD0)
/QSPI_SD1: U4.2 (DO_IO1), U7.55 (QSPI_SD1)
/QSPI_SD2: U4.3 (~WP_IO2), U7.54 (QSPI_SD2)
/QSPI_SD3: U4.7 (~HOLD_IO3), U7.51 (QSPI_SD3)
/RTDIN+: C36.1, J11.3, U13.7 (RTDIN+)
/RTDIN-: C36.2, J11.2, U13.8 (RTDIN-)
/RUN: C4.1, R1.2, TP1.1, U7.26 (RUN)
/SPI0_CLK: U7.29 (GPIO18), U13.12 (SCLK), U14.14 (SCL/SCLK)
/SPI0_CS1: U7.28 (GPIO17), U13.13 (~CS)
/SPI0_CS2: U7.31 (GPIO20), U11.1, U14.7 (~CS)
/SPI0_MISO: U7.27 (GPIO16), U13.14 (SDO), U14.12 (SDO/ADDR)
/SPI0_MOSI: U7.30 (GPIO19), U11.2, U13.11 (SDI)
/UART: R27.2, U7.16 (GPIO13), U12.14 (PDN_UART)
/X-: R12.1, U7.36 (GPIO24)
GND: C1.2, C2.2, C3.2, C4.2, C5.2, C6.2, C8.2, C9.2, C10.2, C11.2, C12.2, C13.2, C14.2, C15.2, C16.2, C17.2, C18.2, C19.2, C20.2, C21.2, C22.2, C23.2, C24.2, C25.1, C26.2, C27.1, C28.1, C29.2, C30.2, C31.2, C32.2, C35.2, D1.2 (A), D4.1 (A1), D6.1 (A1), J1.2, J2.3, J2.MP (MountPin), J4.2, J4.MP (MountPin), J5.1, J6.2, J6.MP (MountPin), J7.2, J7.MP (MountPin), J8.3, J8.MP (MountPin), J10.2, J10.MP (MountPin), J11.MP (MountPin), JP3.3 (B), Q1.2 (S), Q2.2 (S), Q3.1 (S), Q3.2 (S), Q3.3 (S), R3.2, R13.2, R17.2, R18.2, R19.2, R21.2, R27.1, R29.2, R30.2, U1.2 (GND), U2.1 (GND), U3.1 (GND), U4.4 (GND), U5.2 (GND), U6.2 (GND), U7.19 (TESTEN), U7.57 (GND), U8.2 (GND), U9.2 (VSS), U9.7 (VSS), U10.7 (R), U10.8 (VSS), U10.9 (VSS), U11.3 (GND), U12.3 (GND), U12.13 (CLK), U12.18 (GND), U12.29 (EPAD), U13.10 (GND), U13.15 (DGND), U13.16 (GND), U13.21 (GND), U14.2 (GND), U14.4 (GND), U14.5 (GND), Y1.2
unnamed: C7.1, D1.1 (K), L1.1, U1.6 (SW)
unnamed: C7.2, U1.1 (CB)
unnamed: C11.1, D2.2 (A), R6.2, R7.2
unnamed: C13.1, J4.1, R9.2, R12.2
unnamed: C17.1, J6.1, R14.2, R15.2
unnamed: C28.2, U12.8 (5VOUT)
unnamed: C31.1, FB1.2, U13.20 (VDD)
unnamed: C33.1, U12.6 (VCP)
unnamed: C34.1, U12.4 (CPO)
unnamed: C34.2, U12.5 (CPI)
unnamed: D2.1 (K), J2.2
unnamed: D3.1 (K), Q1.1 (G), U6.6
unnamed: D3.2 (A), J7.4
unnamed: D5.1 (K), Q2.1 (G), U6.4
unnamed: D5.2 (A), J10.4
unnamed: J3.1, R5.1
unnamed: J5.2, R10.1
unnamed: J5.3, R8.2
unnamed: J7.1, JP1.2 (C)
unnamed: J7.3, Q1.3 (D)
unnamed: J8.2, U8.6
unnamed: J9.1, Q3.5 (D)
unnamed: J10.1, JP2.2 (C)
unnamed: J10.3, Q2.3 (D)
unnamed: Q3.4 (G), U8.4
unnamed: R2.2, R3.1, U1.3 (FB)
unnamed: R8.1, U5.6 (I/O1)
unnamed: R10.2, U5.4 (I/O2)
unnamed: R11.1, U7.21 (XOUT)
unnamed: R11.2, Y1.3
unnamed: R21.1, U10.2 (ADDR)
unnamed: R24.2, R28.2, U12.2 (ENN)
unnamed: R25.2, U12.16 (STEP)
unnamed: R26.2, U12.19 (DIR)
unnamed: R29.1, U12.23 (BRA)
unnamed: R30.1, U12.27 (BRB)
unnamed: R31.1, U13.1 (BIAS), U13.2 (REFIN+)
unnamed: R31.2, U13.3 (REFIN-), U13.4 (ISENSOR)
unnamed: U7.20 (XIN), Y1.1
unnamed: U11.4, U14.13 (SDA/SDI/SDIO)

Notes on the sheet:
Unused
Make sure 1uF is close to pin 44 of RP2040
CHIP | CIN |CBOOST | L | D | RFBt | RFBb BL9342 | 4.7u |0.1u | 6.2u | | 124K | 8.87K LMR54410 | 22u |0.1u | 15u | NC | 309K | 22.1K LMR14006Y | 4.7u |0.1u | 18u | | 88.7K | 6.04K
Make sure 1uF is close to pin 45 of RP2040

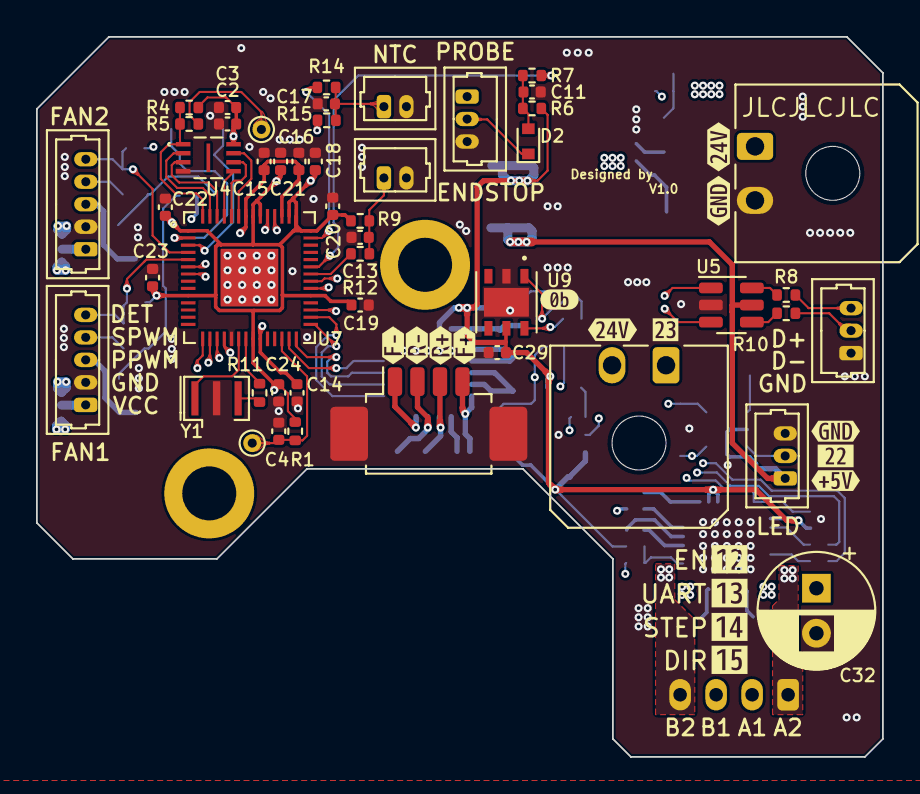
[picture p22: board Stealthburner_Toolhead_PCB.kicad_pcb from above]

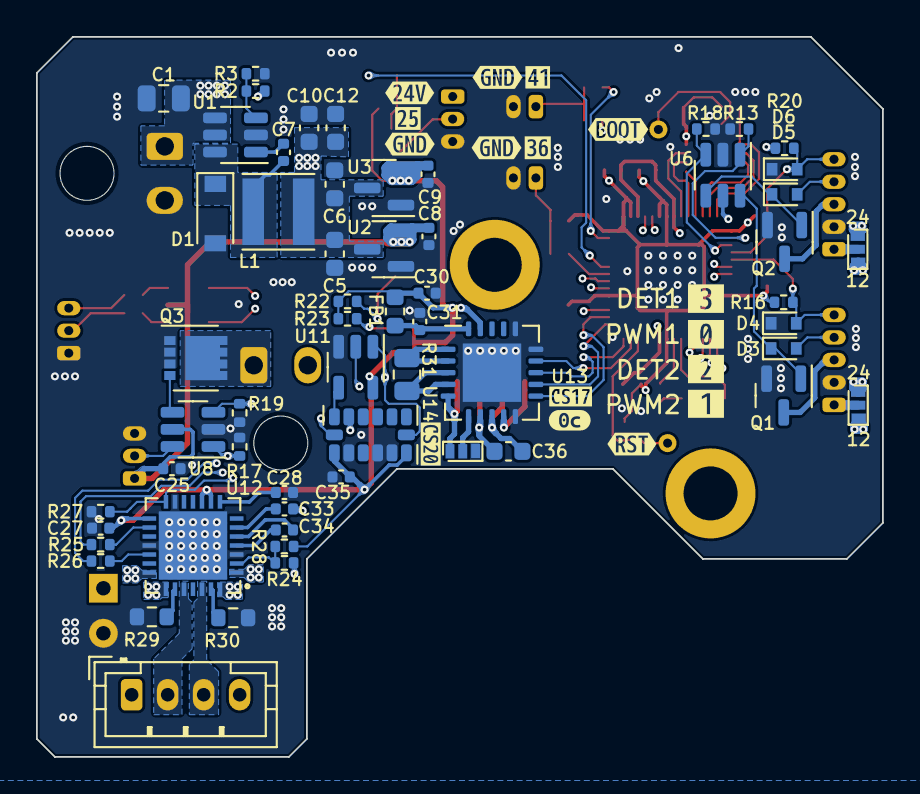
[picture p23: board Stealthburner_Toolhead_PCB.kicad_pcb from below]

Board: 4 copper layers, 47.0 x 40.0 mm, 140 parts (74 on the bottom side), 83 nets.

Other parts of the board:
kibuzzard-62BB1C3A: G***; kibuzzard-62BB1C3A
kibuzzard-62BB1DD3: G***; kibuzzard-62BB1DD3
kibuzzard-62BB1FE0: G***; kibuzzard-62BB1FE0
kibuzzard-62BB1FE5: G***; kibuzzard-62BB1FE5
kibuzzard-62BB1FE8: G***; kibuzzard-62BB1FE8
kibuzzard-62BB1FEC: G***; kibuzzard-62BB1FEC
kibuzzard-62BB238A: G***; kibuzzard-62BB238A
kibuzzard-62BB238F: G***; kibuzzard-62BB238F
kibuzzard-62BB2156: G***; kibuzzard-62BB2156
kibuzzard-62BB2169: G***; kibuzzard-62BB2169
kibuzzard-62BB2226, kibuzzard-62BB2226#2, kibuzzard-62BB2226#3: G***; kibuzzard-62BB2226
kibuzzard-62BB2232, kibuzzard-62BB2232#2, kibuzzard-62BB2232#3, kibuzzard-62BB2232#4: G***; kibuzzard-62BB2232
kibuzzard-62BB2280: G***; kibuzzard-62BB2280
kibuzzard-62BB2393: G***; kibuzzard-62BB2393
kibuzzard-62BB2397: G***; kibuzzard-62BB2397
kibuzzard-62BB2432: G***; kibuzzard-62BB2432
kibuzzard-62BB2448: G***; kibuzzard-62BB2448
kibuzzard-62BB2459: G***; kibuzzard-62BB2459
kibuzzard-62BD8A5A: G***; kibuzzard-62BD8A5A
kibuzzard-62BD8A5E: G***; kibuzzard-62BD8A5E
kibuzzard-62BD8A50: G***; kibuzzard-62BD8A50
kibuzzard-62BD8A57: G***; kibuzzard-62BD8A57
kibuzzard-62BD8C8D: G***; kibuzzard-62BD8C8D
kibuzzard-62BD8C64: G***; kibuzzard-62BD8C64
kibuzzard-62BD8821: G***; kibuzzard-62BD8821
kibuzzard-62BD8832: G***; kibuzzard-62BD8832
kibuzzard-62BD8846: G***; kibuzzard-62BD8846

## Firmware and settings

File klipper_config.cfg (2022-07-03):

[mcu rp2040]
serial: /dev/serial/by-id/usb-Klipper_rp2040_E660D051138A3B35-if00
restart_method: command

[neopixel toolhead_rgb]
pin: rp2040:gpio22
chain_count: 3
color_order: GRB
initial_RED: 0.3 
initial_GREEN: 0.3
initial_BLUE: 0.3

[heater_fan hotend_fan]
pin: rp2040:gpio0
heater: extruder
heater_temp: 50.0
tachometer_pin: rp2040:gpio3
tachometer_ppr: 2
tachometer_poll_interval: 0.0015

[fan]
pin: rp2040:gpio1
tachometer_pin: rp2040:gpio2
tachometer_ppr: 2
tachometer_poll_interval: 0.0015

[temperature_sensor SHT20]
sensor_type: SHT21
i2c_mcu: rp2040
i2c_bus: i2c0b

[extruder]
step_pin: rp2040:gpio14
dir_pin: !rp2040:gpio15
enable_pin: rp2040:gpio12
microsteps: 16
rotation_distance: 33.500
nozzle_diameter: 0.4
filament_diameter: 1.75
heater_pin: rp2040:gpio23

sensor_type: MAX31865
sensor_pin: rp2040:gpio17
spi_bus: spi0c
rtd_nominal_r: 100.0
rtd_reference_r: 430.0
rtd_num_of_wires: 2
min_temp:  -30
max_temp: 450

#sensor_type: ATC Semitec 104GT-2
#sensor_pin: rp2040:gpio41

control: pid
pid_Kp: 22.2
pid_Ki: 1.08
pid_Kd: 114
max_extrude_cross_section: 2


[tmc2209 extruder]
uart_pin: rp2040:gpio13
uart_address: 3
run_current: 0.650
hold_current: 0.500
#stealthchop_threshold: 999999

[probe]
pin: rp2040:gpio25
x_offset: 0.0
z_offset: 0.0
y_offset: 0.0
speed: 40

[stepper_x]
endstop_pin: rp2040:gpio36

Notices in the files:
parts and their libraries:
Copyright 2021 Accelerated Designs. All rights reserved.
